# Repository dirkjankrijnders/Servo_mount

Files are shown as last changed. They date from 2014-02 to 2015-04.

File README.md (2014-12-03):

Servo mount
===========

Based on several threads on the dutch three-rail model railroad forum (for example [here](http://forum.3rail.nl/index.php?topic=36707.msg814683#msg814683)), I came up with the idea to combine a PCB of say a decoder with the mechanical mounting of a servo. (cheap to manufacture on small scale and very precise). The result:

Revision 1
----------
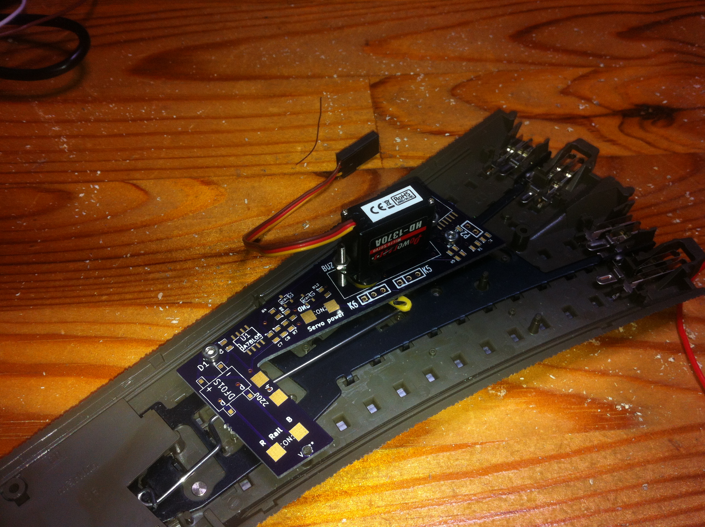
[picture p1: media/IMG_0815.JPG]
First servo mounted!


The design is based on the [PSSD](https://github.com/dirkjankrijnders/PSSD), however using a different microcontroller (attiny84) for more memory options and smaller footprint. The construction also meant sacrificing the buttons, so another way of programming the decoder was needed. The ISP connector already planned also has the I2C lines available, so the decoder can now be configured by setting registers over I2C. An arduino sketch facilitates this process.

The decoder has not yet been tested on the PCB, but works on the breadboard. It support two servo's, so only half of the PCB's need their components placed, the second servo can be connected via standard servo wires.

Revision 2
----------
I already found some issues with the electronics side of the decoder, so a second revision is planned. The second revision fixes most footprint issues as well as allowing mount in both left and right switches. Also all components have been moved to the back of the PCB so the build decoder should flush in the C rail ballast form. A good count of the I/O ports shows that there are three unused, these could be used for manual switch buttons.

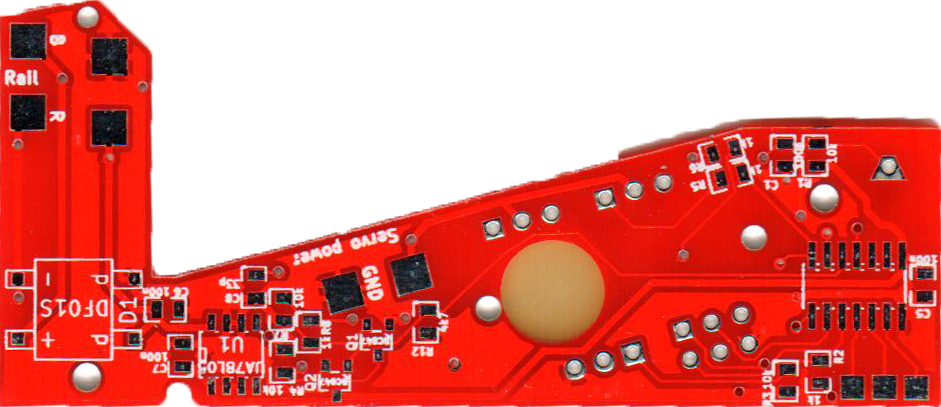
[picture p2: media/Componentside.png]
Second revision boards

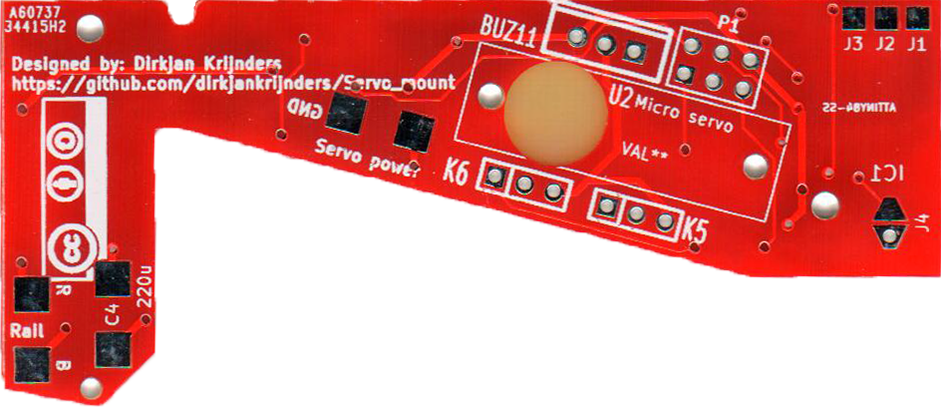
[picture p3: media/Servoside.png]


What is missing? Exactly, the hole for the servo. But a drill can fix that, the 3rd revision will have a hole with the proper shape. Drilling the hole however severed some traces, so those have to be botched, also fixed in the third revision.

After those mechanical problems the electronics all work! So the work on the firmware commenced in full, as per August 16th speed control and a programmer for the I2C interface have been implemented. The manual switch button remain to be implemented.

Revision 3
----------
PCB's for rev.3 were ordered on December 2nd and the changes are:
- Footprint for G-90 servo's
- More I/O pads
- Shape changes to fit under 2471? switches
- moved the solder pads of C4 and the rail power as to not make short-cut contact when the lever passes.

Pictures follow when the boards arrive
Cost/BOM
--------

<table>
<tr>
<th>Part</th><th>#</th><th>Reichelt #</th><th>price* (€)</th>
</tr>
<tr><td>IC1</td><td>1</td><td>ATTINY 44A-SSU</td><td>1.07</td></tr>
<tr><td>D1</td><td>1</td><td>SMD DF 005</td><td>0.18</td></tr>
<tr><td>U1</td><td>1</td><td>µA 78L05 SMD</td><td>0.15</td></tr>
<tr><td>U2</td><td>1</td><td>BUZ 11</td><td>0.57</td></tr>
<tr><td>R*,C*</td><td>2</td><td></td><td>0.50**</td></tr>
<tr><td>PCB</td><td>1</td><td>Seeed</td><td>1.00</td></tr>
<tr><td colspan=3>Total</td><td>3.47</td></tr>
</table>
\* Estimate for orders of 10.<br/>
\** SMD 0805 Components from cost almost nothing in bulk (&gt; 10)

Firmware
--------
To make to PSSD firmware:

	make BOARD=CSMD

To set the fuse and program both flash and eeprom:

	avrdude -p t44 -U lfuse:w:0xe2:m -U hfuse:w:0xdf:m -U efuse:w:0xff:m
	make flash BOARD=CSMD

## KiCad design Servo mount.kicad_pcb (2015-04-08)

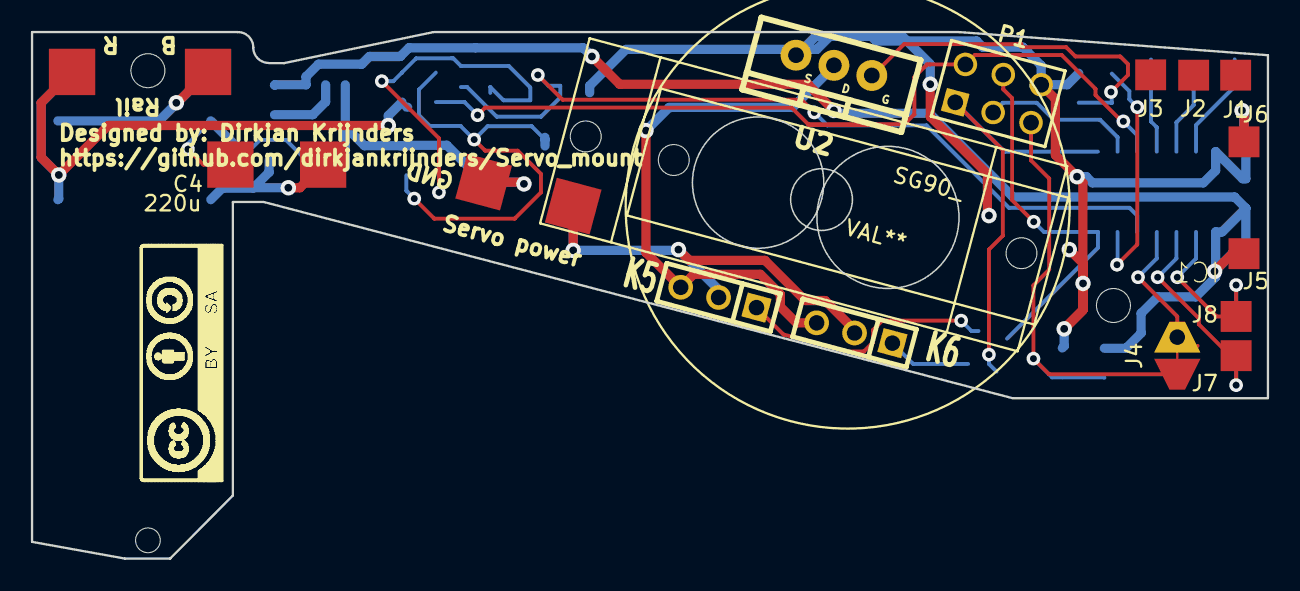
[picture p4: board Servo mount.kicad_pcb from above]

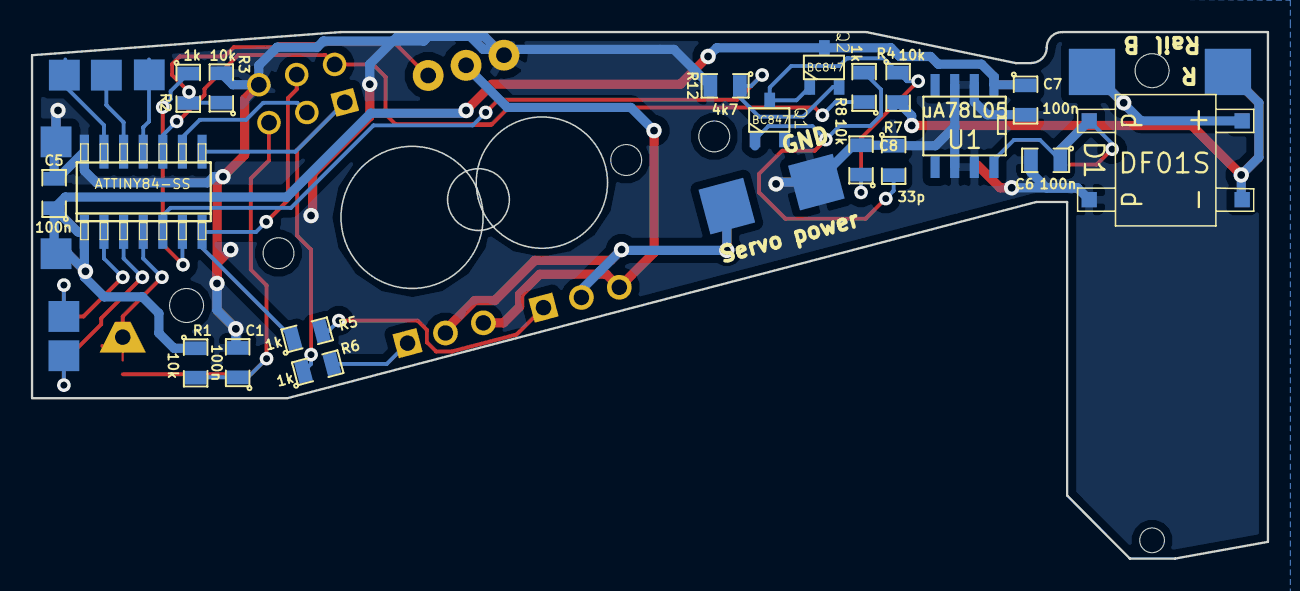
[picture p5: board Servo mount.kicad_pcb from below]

Board: 2 copper layers, 80.0 x 34.1 mm, 33 parts (19 on the bottom side), 24 nets.

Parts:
C1, C5, C6, C7: 100n; SM0805
C4: 220u; Solderpad_2
C8: 33p; SM0805
D1: DF01S; DIPSMD4
IC1: ATTINY84-SS; SOIC-14
J1, J2, J3, J5, J6, J7, J8: SOLDER_PAD; solder_pad_2mm_fb
J4: solder_jumper_conn
K5, K6: CONN_3; SIL-3
P1: CONN_3X2; pin_array_3x2
Q1, Q2: BC847; SOT23
R1, R3, R4, R7: 10k; SM0805
R2, R5, R6, R8: 1k; SM0805
R12: 4k7; SM0805
SG90_: VAL**; Combined_servo
U1: uA78L05; SO8E
U2: BUZ11; TO-220_FET-GDS_Vertical

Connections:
+5V: C5.1, C7.1, IC1.1, J5.1, Q2.3, R1.1, U1.1
AGND: K5.3, K6.3, U2.2
DIS_SIGNAL: IC1.10, P1.2, R8.1
GND: C1.2, C4.2, C5.2, C6.2, C7.2, C8.2, D1.1, IC1.14, J6.1, P1.6, Q1.2, R3.2, R7.1, R12.2, U1.2, U1.3, U1.6, U1.7, U2.3
GND FET: IC1.6, R2.1
MISO: IC1.8, P1.1, R6.1
MOSI: IC1.7, P1.4, R5.1
unnamed: C4.1, C6.1, D1.3, U1.8
unnamed: C8.1, Q1.3, Q2.1, R4.1
unnamed: IC1.2, J8.1
unnamed: IC1.3, J7.1
unnamed: IC1.4, J4.2
unnamed: IC1.11, J3.1
unnamed: IC1.12, J2.1
unnamed: IC1.13, J1.1
unnamed: K5.1, R5.2
unnamed: K6.1, R6.2
unnamed: Q1.1, R7.2, R8.2
unnamed: R2.2, R3.1, U2.1
Rail signal: IC1.5, Q2.2, R12.1
Reset: C1.1, J4.1, P1.5, R1.2
SCK: IC1.9, P1.3
VAA: D1.4, R4.2
VCC: K5.2, K6.2

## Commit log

2013-11-07 Restored AVR ISP Programming, started PCB layout
    [Servo mount.kicad_pcb, Servo mount.sch]
2013-11-18 Layed out board
    [Servo mount.kicad_pcb, Servo mount.sch]
2014-02-18 Rev. 0 as send to OSHPark
    [Servo mount.kicad_pcb, Servo mount.sch]
2014-02-18 Image of prototype
2014-02-25 Changed SOIC-14w to SOIC-14
    Close #3
    [Servo mount.kicad_pcb]
2014-03-06 Fixed rectifier pinout, added front ground plane, closes #2
    [Servo mount.kicad_pcb]
2014-03-06 Updated read me with BOM, closes #5
2014-03-11 Solderpads for I/O (closes #1), reset solder jumper
    Added solder pads for remaining I/O pins on the microcontroller, closes
    #1
    Change the reset jumper to a normally connected solder jumper with
    through hole for debug wire.
    [Servo mount.kicad_pcb, Servo mount.sch]
2014-03-13 Updated schematic to fix wrong servo pins
    [Servo mount.sch]
2014-03-13 Fixed servo connection pins (closes #8) and servo connector holes (closes #6)
    [Servo mount.kicad_pcb]
2014-03-13 Fixed DRC errors
    [Servo mount.kicad_pcb]
2014-03-20 Final board shape, new kicad version
    [Servo mount.kicad_pcb, Servo mount.sch]
2014-05-21 Fixed rev 1 issues
    - Moved all pad away from foot to allow for mounting under crossing
    - Fixed the “hole” for the servo
    - Fixed the order of J4 to really allow debug wire access
    [Servo mount.kicad_pcb, Servo mount.sch]
2014-08-16 Moved tracks away from servo hole
    [Servo mount.kicad_pcb]
2014-08-18 Fixed GND connection servo, fixed TO220 footprint
    [Servo mount.kicad_pcb]
2014-08-20 Clean schematic library
2014-08-20 - Updated schematic to the new standard libraries
    [Servo mount.kicad_pcb, Servo mount.sch]
2014-09-04 Adapted Board shape to 247?? points
    [Servo mount.kicad_pcb]
2014-10-25 Adepted PCB shape for 24712
    [Servo mount.kicad_pcb]
2014-10-29 Updated shape for 24712, made more GND connections
    [Servo mount.kicad_pcb]
2014-11-03 Brought out more I/O, option for larger servo
    [Servo mount.kicad_pcb, Servo mount.sch]
2014-11-03 fix footprints Q1 and Q2
    [Servo mount.kicad_pcb, Servo mount.sch]
2014-11-22 Panel with two PCB's and the combined footprint for SG-90 and micro- Servo's
    [panel.kicad_pcb]
2014-12-03 Updates to rev. 3x
    [Servo mount.kicad_pcb]
2015-04-08 Added production files for rev.3
    [Servo mount-B_Cu.gbr, Servo mount-B_Mask.gbr, Servo mount-B_Paste.gbr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]
2015-11-23 Reconnected wires after library upgrade
    [Servo mount.sch]
2015-11-23 Reconnected wire after library upgrade
